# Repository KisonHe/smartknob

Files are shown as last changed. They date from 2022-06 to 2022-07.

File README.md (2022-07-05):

# SmartKnob
SmartKnob is an open-source input device with software-configurable endstops and virtual detents.

A brushless gimbal motor is paired with a magnetic encoder to provide closed-loop torque feedback control, making it possible to dynamically create and adjust the feel of detents and endstops.




# Designs

## SmartKnob View
Premium SmartKnob experience. Under active development.

⚠️ **As a result of the popularity of this project, it seems like the recommended motors are unfortunately no longer available.** I expect that these motors are simply no longer in production and therefore limited stock was available. However... 👇

💡 **There is an ongoing search for new motors** and I am currently in talks with what appears to be the original motor manufacturer about getting new motors manufactured (updated as of 2022-06-26). A summary of the motor search is being kept up to date in the [wiki](https://github.com/scottbez1/smartknob/wiki/Motor-Status), and there's a long discussion in [issue #16](https://github.com/scottbez1/smartknob/issues/16) - follow along there for the latest info (or join in and help us find a good replacement, but please check the wiki to see if your suggestion has already been mentioned before posting your own comment!). Any change in motor will likely require substantial redesigns, so *don't order PCBs/printed parts until there is more clarity on the motor.*

Features:
 - 240x240 round LCD ("GC9A01"), protected by 39.5mm watch glass on rotor
 - BLDC gimbal motor, with a hollow shaft for mechanically & electrically connecting the LCD
 - Powered by ESP32-PICO-V3-02 (Lilygo TMicro32 Plus module)
 - PCB flexure and strain gauges used for press detection (haptic feedback provided via the motor)
 - 8 side-firing RGB LEDs (SK6812-SIDE-A) illuminate ring around the knob
 - USB-C (2.0) connector for 5V power and serial data/programming (CH340)
 - VEML7700 ambient light sensor for automatic backlight & LED intensity adjustment
 - Versatile back plate for mounting - use either 4x screws, or 2x 3M medium Command strips (with cutouts for accessing removal tabs after installation)
 - Front cover snaps on for easy access to the PCB

**Current status:** Not recommended for general use (mechanical and electrical revisions may be needed depending on motor/electronics availability)

### Demo video

<a href="https://www.youtube.com/watch?v=ip641WmY4pA">
    
</a>

### How it works
<a href="https://www.youtube.com/watch?v=Q76dMggUH1M">
    
</a>

### 3D CAD

Exploded view

Latest Fusion 360 Model: https://a360.co/3BzkU0n

### Build your own?

While this is a "DIY" open-source project, it is not yet a mature plug-and-play project. If you intend to build your own, note that it requires advanced soldering experience to build - very small-pitch surface-mount soldering is required (reflow or hot air recommended), and assembly is quite time-consuming and delicate. Please go into it with the expectation that you will almost certainly need to be able to troubleshoot some hardware and firmware issues yourself - I recommend reviewing/understanding the schematics and basic firmware before jumping in!

More documentation on the BOM and what parts you need to order is coming in the future - thanks so much for your interest! Follow me on [Twitter](https://twitter.com/scottbez1) for the latest updates on this and other projects.

View the latest auto-generated (untested) [Base PCB Interactive BOM](https://smartknob-artifacts.s3.us-west-1.amazonaws.com/master/electronics/view_base-ibom.html) and [Screen PCB Interactive BOM](https://smartknob-artifacts.s3.us-west-1.amazonaws.com/master/electronics/view_screen-ibom.html) (or, the combined [BOM csv](https://smartknob-artifacts.s3.us-west-1.amazonaws.com/master/electronics/view_base-bom.csv)) for electronics/hardware parts list. ⚠️ These are auto-generated from the latest untested revision on GitHub. For tested/stable/recommended artifacts, use a [release](https://github.com/scottbez1/smartknob/releases) instead.

A few miscellaneous notes in the meantime:

 - This can _probably_ be FDM 3D printed with a well-tuned printer, but the parts shown in videos/photos were MJF printed in nylon for tight tolerances and better surface finish
 - If you wanted a simpler build, you could omit the LCD and just merge the knob + glass from the model into a single STL to get a closed-top knob
 - There's limited space inside the LCD mount for wiring, and 8 wires need to fit through the hole in the center. I used 30 AWG wire-wrapping wire. Enamel-coated wire would probably work too.
 - Strain gauges are BF350-3AA, and glued in place with CA glue (I'll include video of this process in the future, but essentially I used kapton tape to pick up the strain gauge and hold it in place during curing). This has to be done after reflow soldering, and would be hard to remove/fix in case of a mistake, so MAKE SURE TO PRACTICE GLUING strain gauges to other items before attempting on the PCB!
 - The TMC6300 is _tiny_ and has a bottom pad, so I would seriously consider getting a stencil along with the PCB order. Even with the stencil I needed to manually clean up some bridging afterward; I _highly_ recommend Chip Quik NC191 gel flux, available on [Amazon](https://amzn.to/3MGDSr5) (or use this [non-affiliate link](https://www.amazon.com/Smooth-Flow-No-Clean-syringe-plunger/dp/B08KJPG3NZ) instead) or from your electronics distributor of choice. Flux is also very helpful when soldering the LCD ribbon cable to to screen PCB.
 - For breadboard prototyping, the [TMC6300-BOB](https://www.trinamic.com/support/eval-kits/details/tmc6300-bob/) is awesome and way easier to work with than the bare chip if you just want to play around with low current BLDC motors
 - For AliExpress purchases: I highly recommend **only** using AliExpress Standard Shipping (purchasing in the US). I have had multiple purchases take months or never get delivered when purchased with Cainiao or other low cost shipping options, whereas AliExpress Standard is very reliable and generally faster in my experience.
 - Make sure to check the [open issues](https://github.com/scottbez1/smartknob/issues) - this design is not yet "stable", so beware that everything may not go smoothly. I would not recommend ordering these parts yourself until the [stable release v1.0 milestone](https://github.com/scottbez1/smartknob/milestone/1) is complete, as there are some mechanical interference issues in the current revision.

Future plans:
 - consider switch to using an ESP32-S3-MINI-1 module (once Arduino core support is complete), as that would allow for direct USB HID support (for joystick/macro-pad type input to a computer)
 - Bluetooth HID support?
 - get wifi configured and working (probably MQTT?). Currently memory is an issue with the full display framebuffer sprite. PSRAM might fix this (requires newer ESP-IDF & unreleased Arduino core, and from a brief test I got horrible performance with PSRAM enabled), or the next item might help reduce memory:
 - migrate to LVGL, for better display rendering and easy support for menus, etc. Shouldn't require a full 240x240x24b framebuffer in memory, freeing some for wifi, etc.
 - integrate nanopb for structured serial data (see [splitflap protobuf protocol](https://github.com/scottbez1/splitflap/blob/1440aba54d5b0d822ec5da68762431879988d7ef/arduino/splitflap/esp32/splitflap/serial_proto_protocol.cpp) for example)
 - Home Assistant integration, or other real-world applications
 - ???
 - [Profit](https://github.com/sponsors/scottbez1/) 😉

#### Base PCB

<a href="https://smartknob-artifacts.s3.us-west-1.amazonaws.com/master/electronics/view_base-front-3d.png">
    
</a>
<a href="https://smartknob-artifacts.s3.us-west-1.amazonaws.com/master/electronics/view_base-back-3d.png">
    
</a>

Ordering notes: use white soldermask, for reflecting light from RGB LED ring around the knob. Should be 1.2mm thick (not "standard" 1.6mm).

Latest auto-generated (untested and likely broken!) artifacts⚠️:

[Schematic](https://smartknob-artifacts.s3.us-west-1.amazonaws.com/master/electronics/view_base-schematic.pdf)

[Interactive BOM](https://smartknob-artifacts.s3.us-west-1.amazonaws.com/master/electronics/view_base-ibom.html)

[PCB Packet](https://smartknob-artifacts.s3.us-west-1.amazonaws.com/master/electronics/view_base-pcb-packet.pdf)

[Gerbers](https://smartknob-artifacts.s3.us-west-1.amazonaws.com/master/electronics/view_base-jlc/gerbers.zip)

⚠️ For tested/stable/recommended artifacts, use a [release](https://github.com/scottbez1/smartknob/releases) instead.

#### Screen PCB

<a href="https://smartknob-artifacts.s3.us-west-1.amazonaws.com/master/electronics/view_screen-front-3d.png">
    
</a>
<a href="https://smartknob-artifacts.s3.us-west-1.amazonaws.com/master/electronics/view_screen-back-3d.png">
    
</a>

Ordering notes: Must be 1.2mm thick (not "standard" 1.6mm) per mechanical design.

Latest auto-generated (untested and likely broken!) artifacts⚠️:

[Schematic](https://smartknob-artifacts.s3.us-west-1.amazonaws.com/master/electronics/view_screen-schematic.pdf)

[Interactive BOM](https://smartknob-artifacts.s3.us-west-1.amazonaws.com/master/electronics/view_screen-ibom.html)

[PCB Packet](https://smartknob-artifacts.s3.us-west-1.amazonaws.com/master/electronics/view_screen-pcb-packet.pdf)

[Gerbers](https://smartknob-artifacts.s3.us-west-1.amazonaws.com/master/electronics/view_screen-jlc/gerbers.zip)

⚠️ For tested/stable/recommended artifacts, use a [release](https://github.com/scottbez1/smartknob/releases) instead.

## SmartKnob Mini
Planned for the future.

# Frequently Asked Questions (FAQ)

**How much does it cost?**

I wish I could tell you now, but I don't actually know off the top of my head. Check back soon - I've only built 1 so far, which was the result of a bunch of tinkering and prototyping over an extended period, so I don't have all the expenses tallied up yet. Certainly less than $200 in parts, and maybe closer to $100?

**Does it work with XYZ?**

Not yet. So far I've only implemented enough firmware for the demo shown in the video, so you can't actually use it for anything productive yet. The basic detent configuration API is there, but not much else. Lots of firmware work remains to be done. If you build one, I'd love your help adding support for XYZ though!

**Can I buy one as a kit or already assembled?**

Probably not? Or at least, I don't have any immediate plans to sell them myself. It's not that I don't want you to be happy, but hardware is a hard business and I just work on this stuff in my free time.

It's open source with a fairly permissive license though, so in theory anyone could start offering kits/assemblies. If someone does go down that route of selling them, note that attribution is
 _required_ (and I wouldn't say no to [royalties/tips/thanks](https://github.com/sponsors/scottbez1/) if you're in a giving mood 🙂).

## General Component Info

### Magnetic encoders

#### MT6701 (MagnTek)
Excellent sensor at a reasonable price - highly recommended. Less noisy than TLV493D, and more responsive (control loop is more stable) using SSI.

 - Lots of IO options - SSI, I2C, and ABZ - should offer good response latency
 - SSI includes CRC to validate data
 - No power-down or low-power options - may not be ideal for battery-powered devices
 - Not available from US distributors (Mouser, Digi-Key)

[Datasheet](http://www.magntek.com.cn/upload/MT6701_Rev.1.5.pdf)

[Ordering (LCSC)](https://lcsc.com/product-detail/Angle-Linear-Position-Sensors_Magn-Tek-MT6701CT-STD_C2856764.html)

#### TLV493D (Infineon)
A mediocre choice. Easy to prototype with using [Adafruit's QWIIC breakout board](https://www.adafruit.com/product/4366).

In my testing, it is a little noisy, requiring filtering/smoothing that can slow responsiveness, hurting control loop stability. Or, with less filtering, the noise
can easily be "amplified" by the derivative component in the PID motor torque controller, causing audible (and tactile) humming/buzzing.

There is also apparently a known silicon issue that causes the internal ADC to sometimes completely lock up, requiring a full reset and re-configuration. See section
5.6 in the [User Manual](https://www.infineon.com/dgdl/Infineon-TLV493D-A1B6_3DMagnetic-UM-v01_03-EN.pdf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)

    In the Master Controlled Mode (MCM) or the Fast Mode (FM) the ADC conversion may hang up. A hang up can
    be detected by:
     - Frame Counter (FRM) counter stucks and does not increment anymore.

In my experience testing 4 different Adafruit breakout boards, 2 of them (50%) regularly exhibit this lockup behavior within a minute or two of use. It is possible to detect and auto-reset (and there is code in the project to do so), but it is slow and may cause undesirable jumps/delays if the sensor locks up often.

[Datasheet](https://www.mouser.com/datasheet/2/196/Infineon_TLV493D_A1B6_DataSheet_v01_10_EN-1227967.pdf)

#### AS5600 (AMS)
A mediocre choice. Cheap breakout boards are readily available.

In my testing, it's fairly noisy (anecdotally, noisier than the TLV493d), requiring filtering/smoothing that can slow responsiveness, hurting control loop stability. Additionally, it saturates at a lower magnetic field strength than other sensors I tested, requiring a significant air gap (8-10mm) when used with a strong neodymium diametric magnet like [Radial Magnets 8995](https://www.digikey.com/en/products/detail/radial-magnets-inc/8995/5126077).

[Datasheet](https://ams.com/documents/20143/36005/AS5600_DS000365_5-00.pdf)

### Motor drivers
#### TMC6300-LA
This is a relatively new IC and it's a perfect match! There generally aren't any other drivers (with integrated fets) that meet the requirements for the low-voltage and low-current motors used in this project (DRV8316 might work, but has not been tested).

Highlights:
 - 2-11V DC motor supply input
 - Up to 1.2A RMS
 - Tiny (3x3mm QFN)

 [Datasheet](https://www.trinamic.com/fileadmin/assets/Products/ICs_Documents/TMC6300_datasheet_rev1.07.pdf)

 [Product page](https://www.trinamic.com/products/integrated-circuits/details/tmc6300-la/)

### Motors
#### 32mm Rotor, Hollow Shaft, Diametric magnet



- 32mm rotor
- 15mm overall height (including magnet), 12.75mm height w/o magnet, 9mm rotor height
- low/zero cogging - excellent for completely smooth input
- 5.9mm hollow shaft
- built-in diametric magnet for encoder
- Proven option

This is overall the easiest motor to get started with. Low cogging and a built-in diametric magnet are great!

Sadly, does not seem to be available any longer.

# Firmware
TODO: document this

Also TODO: implement a lot more of the firmware

# Acknowledgements
This project was greatly inspired by Jesse Schoch's video "[haptic textures and virtual detents](https://www.youtube.com/watch?v=1gPQfDkX3BU)" and the
corresponding [discussion in the SimpleFOC community](https://community.simplefoc.com/t/haptic-textures/301). Seriously, this project wouldn't exist if not for that video - thank you Jesse!

# License

This project is licensed under Apache v2 (software, electronics, documentation) and Creative Commons Attribution 4.0 (hardware/mechanical) (see [LICENSE.txt](LICENSE.txt) and [Creative Commons](https://creativecommons.org/licenses/by/4.0/)).

    Copyright 2022 Scott Bezek
    
    Licensed under the Apache License, Version 2.0 (the "License");
    you may not use this file except in compliance with the License.
    You may obtain a copy of the License at
    
        http://www.apache.org/licenses/LICENSE-2.0
    
    Unless required by applicable law or agreed to in writing, software
    distributed under the License is distributed on an "AS IS" BASIS,
    WITHOUT WARRANTIES OR CONDITIONS OF ANY KIND, either express or implied.
    See the License for the specific language governing permissions and
    limitations under the License.

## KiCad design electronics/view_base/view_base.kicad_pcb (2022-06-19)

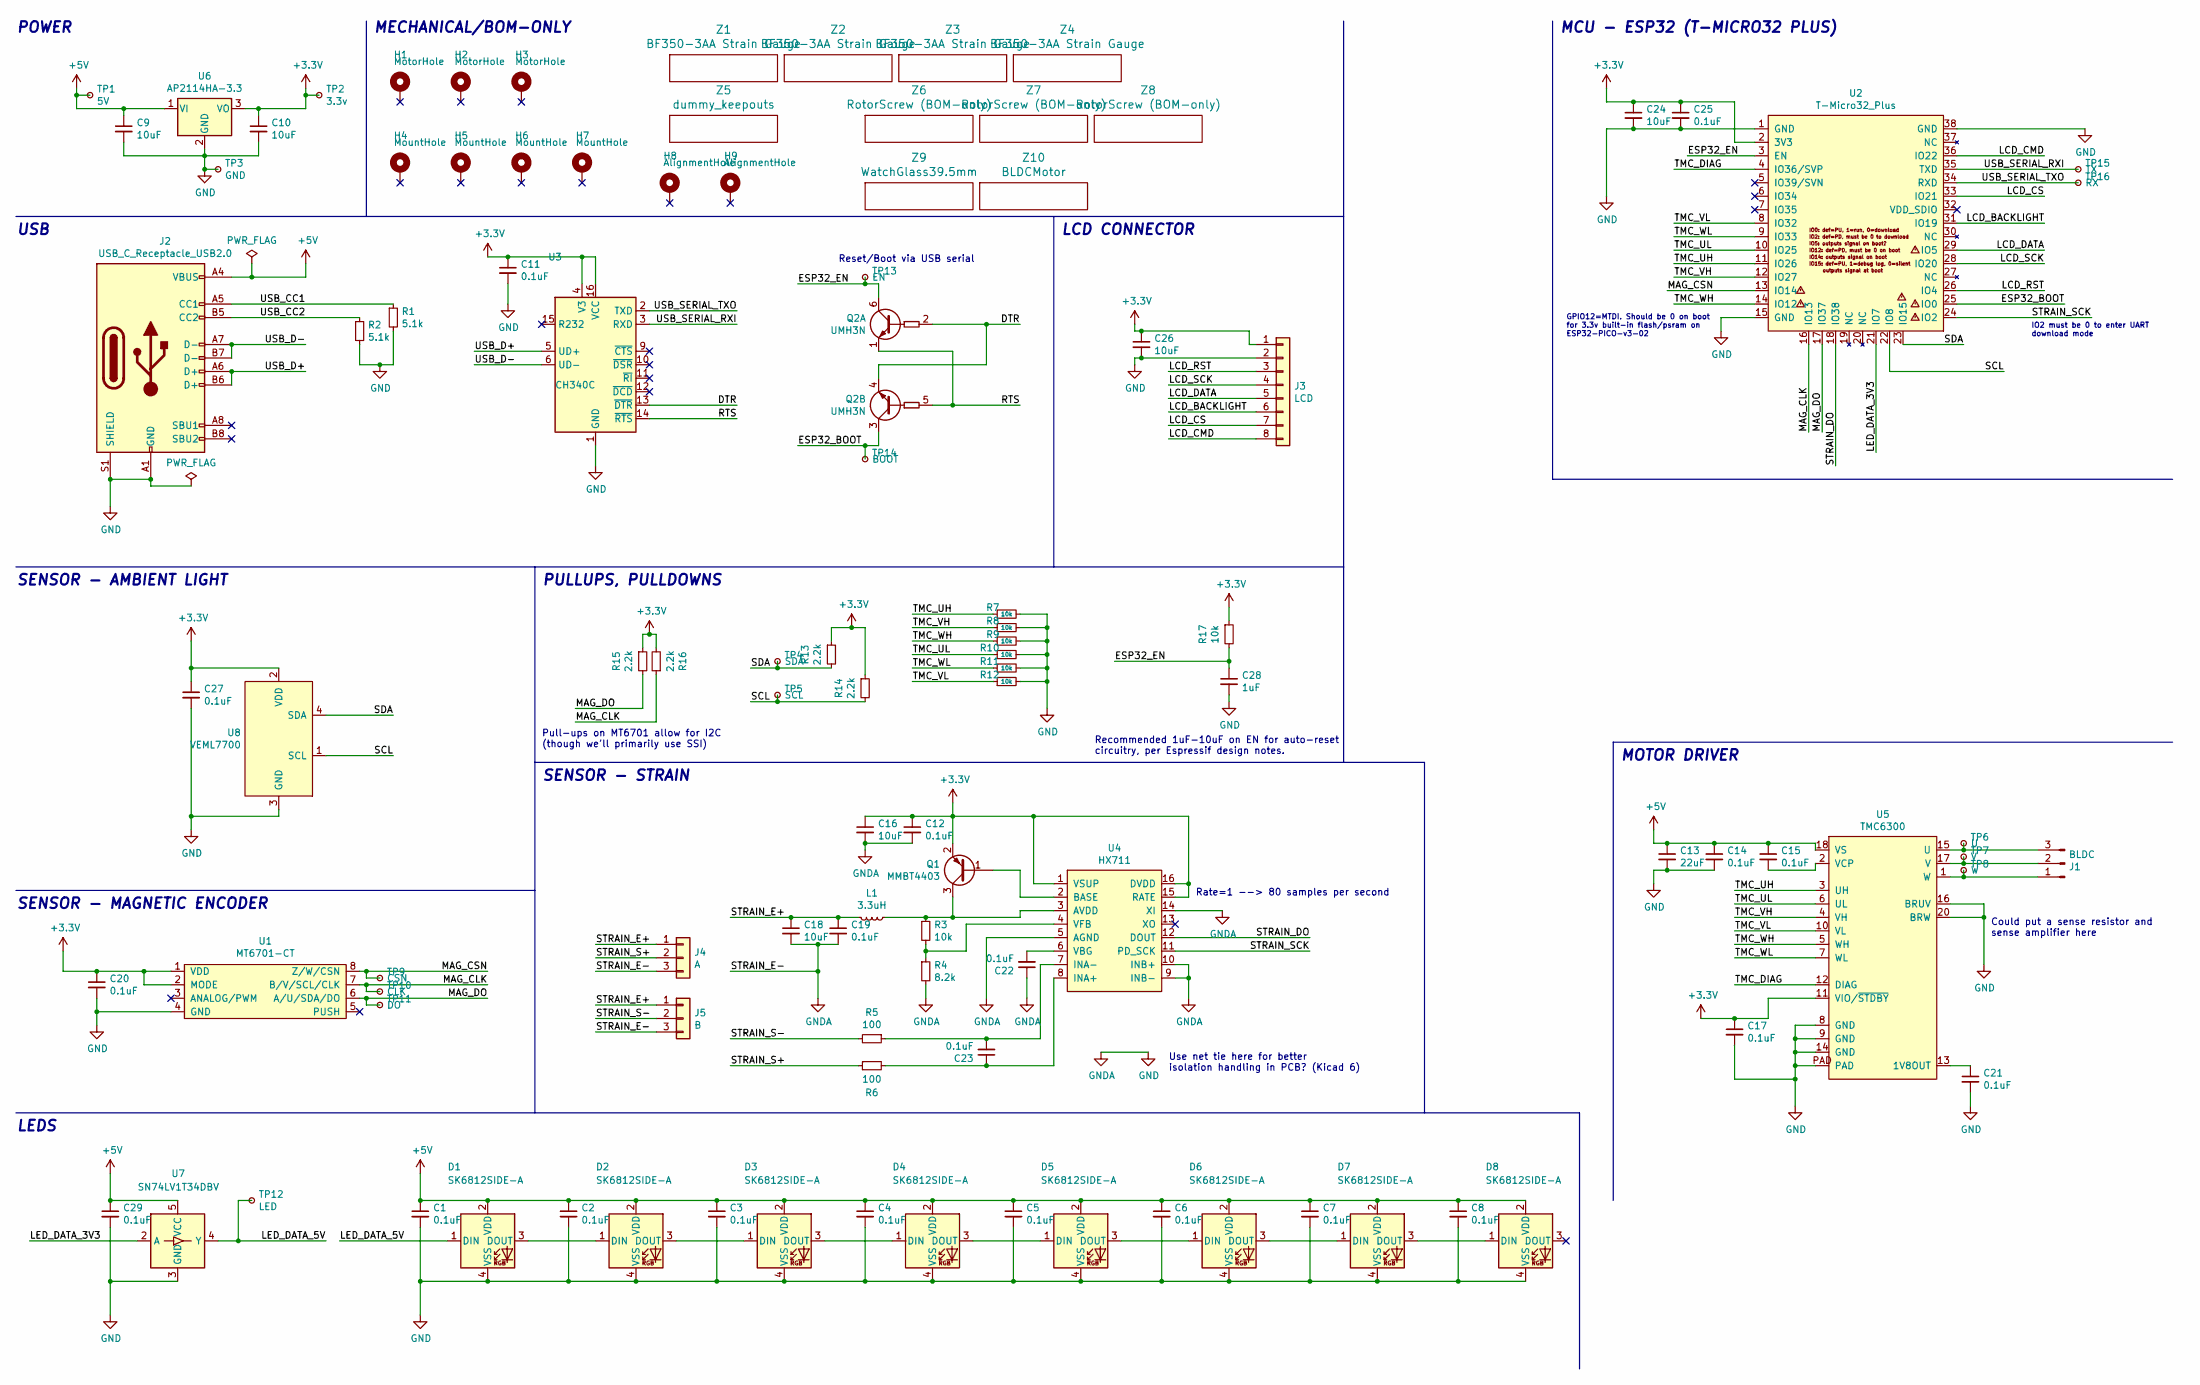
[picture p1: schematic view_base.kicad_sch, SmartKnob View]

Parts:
C1, C2, C3, C4, C5, C6, C7, C8, C11, C12, C14, C15, C17, C19, C20, C21, C22, C23, C25, C27, C29: 0.1uF; C_0603_1608Metric; LCSC C1591
C9, C10, C16, C18, C24, C26: 10uF; C_0805_2012Metric; LCSC C2922480
C13: 22uF; C_0805_2012Metric; LCSC C98190
C28: 1uF; C_0603_1608Metric; Mouser 187-CL10A105KA8NNNC
D1, D2, D3, D4, D5, D6, D7, D8: SK6812SIDE-A; SK6812-SIDE-A; Digikey 1528-4691-ND
H1, H2, H3: MotorHole; MountingHole_M1.6
H4, H5, H6, H7: MountHole; MountingHole_2.2mm_M2_ISO7380_Pad_NonVirtual
H8, H9: AlignmentHole; MountingHole_2.2mm_M2_ISO7380_Pad_NonVirtual
J1: BLDC; 532610371; LCSC C293630
J2: USB_C_Receptacle_USB2.0; USB4510_NoPaste; LCSC C428463
J3: LCD; SolderPads_2mm_8
J4: A; SolderPads_2mm_3_STRAIN
J5: B; SolderPads_2mm_3_STRAIN
L1: 3.3uH; L_0805_2012Metric; LCSC C307744
Q1: MMBT4403; SOT-23; LCSC C78864
Q2: UMH3N; SOT-363_SC-70-6; LCSC C62892
R1, R2: 5.1k; R_0603_1608Metric; LCSC C105580
R3, R7, R8, R9, R10, R11, R12, R17: 10k; R_0603_1608Metric; LCSC C98220
R4: 8.2k; R_0603_1608Metric; LCSC C114637
R5, R6: 100; R_0603_1608Metric; LCSC C319953
R13, R14, R15, R16: 2.2k; R_0603_1608Metric; LCSC C4190
TP1: 5V; TestPoint_Pad_D2.0mm_ValueSilk
TP2: 3.3v; TestPoint_Pad_D2.0mm_ValueSilk
TP3: GND; TestPoint_Pad_D2.0mm_ValueSilk
TP4: SDA; TestPoint_Pad_D2.0mm_ValueSilk
TP5: SCL; TestPoint_Pad_D2.0mm_ValueSilk
TP6: U; TestPoint_Pad_D2.0mm_ValueSilk
TP7: V; TestPoint_Pad_D2.0mm_ValueSilk
TP8: W; TestPoint_Pad_D2.0mm_ValueSilk
TP9: CSN; TestPoint_Pad_D2.0mm_ValueSilk
TP10: CLK; TestPoint_Pad_D2.0mm_ValueSilk
TP11: DO; TestPoint_Pad_D2.0mm_ValueSilk
TP12: LED; TestPoint_Pad_D2.0mm_ValueSilk
TP13: EN; TestPoint_Pad_D2.0mm_ValueSilk
TP14: BOOT; TestPoint_Pad_D2.0mm_ValueSilk
TP15: TX; TestPoint_Pad_D2.0mm_ValueSilk
TP16: RX; TestPoint_Pad_D2.0mm_ValueSilk
U1: MT6701-CT; SOIC-8_3.9x4.9mm_P1.27mm; LCSC C2856764
U2: T-Micro32_Plus; T-Micro32; Digikey N/A
U3: CH340C; SOIC-16_3.9x9.9mm_P1.27mm; LCSC C84681
U4: HX711; SOIC-16_3.9x9.9mm_P1.27mm; LCSC C43656
U5: TMC6300; QFN-20-1EP_3x3mm_P0.4mm_EP1.65x1.65mm_ThermalVias_LargerVia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; Digikey TMC6300-LA-T
U6: AP2114HA-3.3; SOT-223-3_TabPin2; LCSC C460314
U7: SN74LV1T34DBV; SOT-23-5; LCSC C100024
U8: VEML7700; VEML7700-TOP; Digikey VEML7700-TT
Z1, Z2, Z3, Z4: BF350-3AA Strain Gauge; BF350-3AA; Digikey N/A
Z5: dummy_keepouts; ViewKeepouts3d
Z6, Z7, Z8: RotorScrew (BOM-only); bom_only_no_pin
Z9: WatchGlass39.5mm; bom_only_no_pin
Z10: BLDCMotor; bom_only_no_pin

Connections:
+3V3: C10.1, C11.1, C12.1, C16.1, C17.1, C20.1, C24.1, C25.1, C26.1, C27.1, J3.1, Q1.2 (E), R13.1, R14.1, R15.1, R16.2, R17.1, TP2.1, U1.1 (VDD), U1.2 (MODE), U2.2 (3V3), U3.4 (V3), U3.16 (VCC), U4.1 (VSUP), U4.15 (RATE), U4.16 (DVDD), U5.11 (VIO/~STDBY), U6.3 (VO), U8.2 (VDD)
+5V: C1.1, C2.1, C3.1, C4.1, C5.1, C6.1, C7.1, C8.1, C9.1, C13.1, C14.1, C15.1, C29.1, D1.2 (VDD), D2.2 (VDD), D3.2 (VDD), D4.2 (VDD), D5.2 (VDD), D6.2 (VDD), D7.2 (VDD), D8.2 (VDD), J2.A4 (VBUS), J2.A9 (VBUS), J2.B4 (VBUS), J2.B9 (VBUS), TP1.1, U5.18 (VS), U6.1 (VI), U7.5 (VCC)
/DTR: Q2.2 (B1), Q2.4 (E2), U3.13 (~DTR)
/ESP32_BOOT: Q2.3 (C2), TP14.1, U2.25 (IO0)
/ESP32_EN: C28.1, Q2.6 (C1), R17.2, TP13.1, U2.3 (EN)
/LCD_BACKLIGHT: J3.6, U2.31 (IO19)
/LCD_CMD: J3.8, U2.36 (IO22)
/LCD_CS: J3.7, U2.33 (IO21)
/LCD_DATA: J3.5, U2.29 (IO5)
/LCD_RST: J3.3, U2.26 (IO4)
/LCD_SCK: J3.4, U2.28 (IO20)
/LED_DATA_3V3: U2.21 (IO7), U7.2 (A)
/LED_DATA_5V: D1.1 (DIN), TP12.1, U7.4 (Y)
/MAG_CLK: R16.1, TP10.1, U1.7 (B/V/SCL/CLK), U2.16 (IO13)
/MAG_CSN: TP9.1, U1.8 (Z/W/CSN), U2.13 (IO14)
/MAG_DO: R15.2, TP11.1, U1.6 (A/U/SDA/DO), U2.17 (IO37)
/RTS: Q2.1 (E1), Q2.5 (B2), U3.14 (~RTS)
/SCL: R14.2, TP5.1, U2.22 (IO8), U8.1 (SCL)
/SDA: R13.2, TP4.1, U2.23 (IO15), U8.4 (SDA)
/STRAIN_DO: U2.18 (IO38), U4.12 (DOUT)
/STRAIN_E+: C18.1, C19.1, J4.1, J5.1, L1.2
/STRAIN_S+: J4.2, R6.1
/STRAIN_S-: J5.2, R5.2
/STRAIN_SCK: U2.24 (IO2), U4.11 (PD_SCK)
/TMC_DIAG: U2.4 (IO36/SVP), U5.12 (DIAG)
/TMC_UH: R7.1, U2.11 (IO26), U5.3 (UH)
/TMC_UL: R10.1, U2.10 (IO25), U5.6 (UL)
/TMC_VH: R8.1, U2.12 (IO27), U5.4 (VH)
/TMC_VL: R12.1, U2.8 (IO32), U5.10 (VL)
/TMC_WH: R9.1, U2.14 (IO12), U5.5 (WH)
/TMC_WL: R11.1, U2.9 (IO33), U5.7 (WL)
/USB_CC1: J2.A5 (CC1), R1.1
/USB_CC2: J2.B5 (CC2), R2.1
/USB_D+: J2.A6 (D+), J2.B6 (D+), U3.5 (UD+)
/USB_D-: J2.A7 (D-), J2.B7 (D-), U3.6 (UD-)
/USB_SERIAL_RXI: TP15.1, U2.35 (TXD), U3.3 (RXD)
/USB_SERIAL_TXO: TP16.1, U2.34 (RXD), U3.2 (TXD)
GND: C1.2, C2.2, C3.2, C4.2, C5.2, C6.2, C7.2, C8.2, C9.2, C10.2, C11.2, C12.2, C13.2, C14.2, C16.2, C17.2, C18.2, C19.2, C20.2, C21.2, C22.1, C24.2, C25.2, C26.2, C27.2, C28.2, C29.2, D1.4 (VSS), D2.4 (VSS), D3.4 (VSS), D4.4 (VSS), D5.4 (VSS), D6.4 (VSS), D7.4 (VSS), D8.4 (VSS), J2.A1 (GND), J2.A12 (GND), J2.B1 (GND), J2.B12 (GND), J2.S1 (SHIELD), J3.2, J4.3, J5.3, R1.2, R2.2, R4.2, R7.2, R8.2, R9.2, R10.2, R11.2, R12.2, TP3.1, U1.4 (GND), U2.1 (GND), U2.15 (GND), U2.38 (GND), U3.1 (GND), U4.5 (AGND), U4.9 (INB-), U4.10 (INB+), U4.14 (XI), U5.8 (GND), U5.9 (GND), U5.14 (GND), U5.16 (BRUV), U5.20 (BRW), U5.PAD, U6.2 (GND), U7.3 (GND), U8.3 (GND)
unnamed: C15.2, U5.2 (VCP)
unnamed: C21.1, U5.13 (1V8OUT)
unnamed: C22.2, U4.6 (VBG)
unnamed: C23.1, R6.2, U4.8 (INA+)
unnamed: C23.2, R5.1, U4.7 (INA-)
unnamed: D1.3 (DOUT), D2.1 (DIN)
unnamed: D2.3 (DOUT), D3.1 (DIN)
unnamed: D3.3 (DOUT), D4.1 (DIN)
unnamed: D4.3 (DOUT), D5.1 (DIN)
unnamed: D5.3 (DOUT), D6.1 (DIN)
unnamed: D6.3 (DOUT), D7.1 (DIN)
unnamed: D7.3 (DOUT), D8.1 (DIN)
unnamed: J1.1, TP8.1, U5.1 (W)
unnamed: J1.2, TP7.1, U5.17 (V)
unnamed: J1.3, TP6.1, U5.15 (U)
unnamed: L1.1, Q1.3 (C), R3.1, U4.3 (AVDD)
unnamed: Q1.1 (B), U4.2 (BASE)
unnamed: R3.2, R4.1, U4.4 (VFB)

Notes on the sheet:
Pull-ups on MT6701 allow for I2C (though we'll primarily use SSI)
Rate=1 --> 80 samples per second
Reset/Boot via USB serial
PULLUPS, PULLDOWNS
SENSOR - AMBIENT LIGHT
MCU - ESP32 (T-MICRO32 PLUS)
MOTOR DRIVER
SENSOR - STRAIN
LEDS
POWER
SENSOR - MAGNETIC ENCODER
USB
IO2 must be 0 to enter UART download mode
Recommended 1uF-10uF on EN for auto-reset circuitry, per Espressif design notes.
MECHANICAL/BOM-ONLY
GPIO12=MTDI. Should be 0 on boot for 3.3v built-in flash/psram on ESP32-PICO-v3-02
LCD CONNECTOR
Use net tie here for better isolation handling in PCB? (Kicad 6)
Could put a sense resistor and sense amplifier here

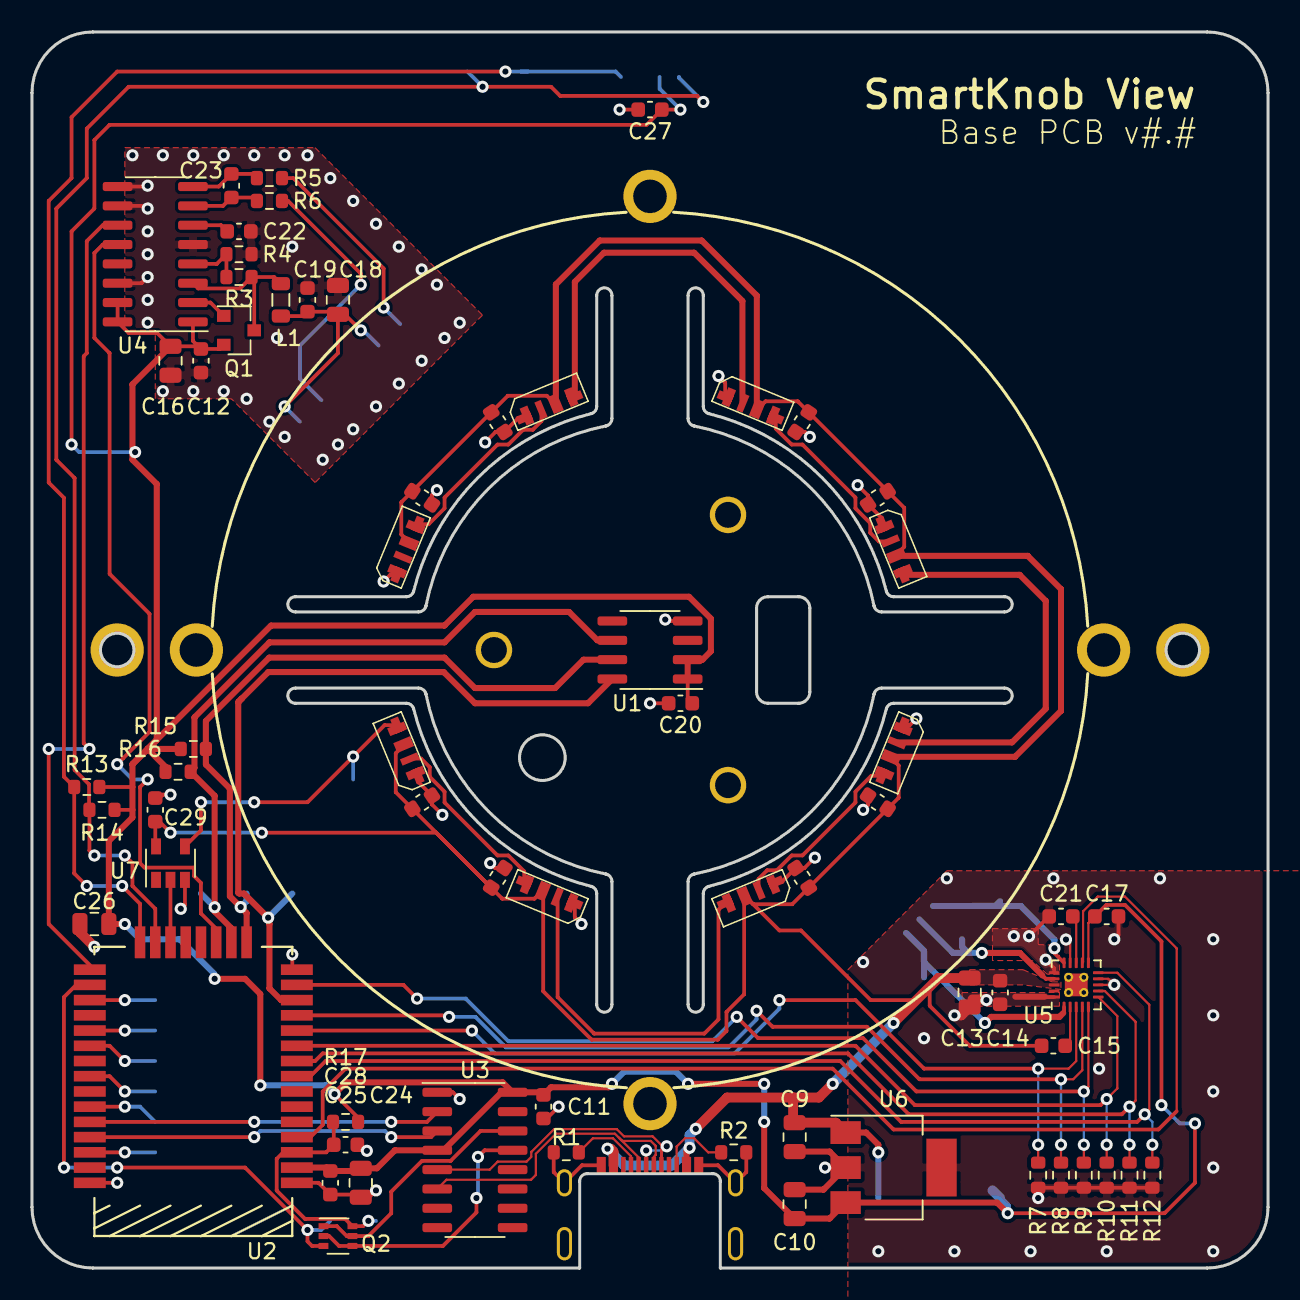
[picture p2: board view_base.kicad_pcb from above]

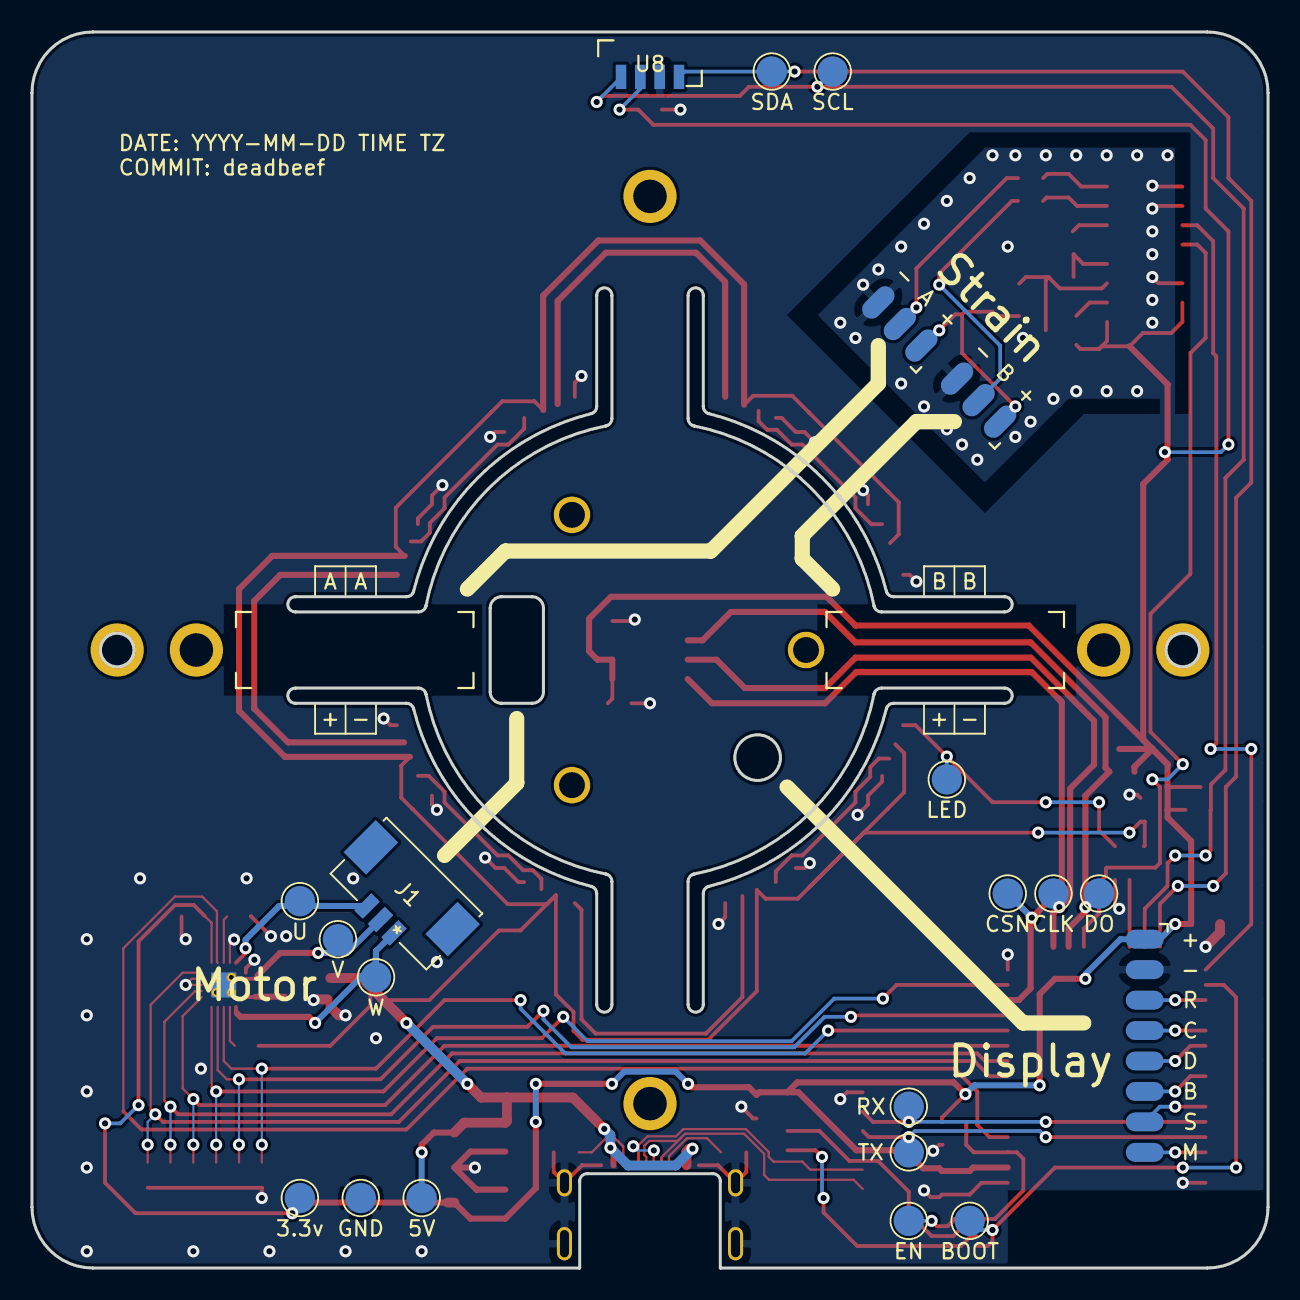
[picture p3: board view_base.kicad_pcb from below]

Board: 2 copper layers, 81.2 x 81.2 mm, 105 parts (25 on the bottom side), 56 nets.

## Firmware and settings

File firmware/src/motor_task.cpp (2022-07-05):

#include <SimpleFOC.h>
#include <sensors/MagneticSensorI2C.h>

#include "motor_task.h"
#include "mt6701_sensor.h"
#include "tlv_sensor.h"
#include "util.h"

static const float DEAD_ZONE_DETENT_PERCENT = 0.2;
static const float DEAD_ZONE_RAD = 1 * _PI / 180;

static const float IDLE_VELOCITY_EWMA_ALPHA = 0.001;
static const float IDLE_VELOCITY_RAD_PER_SEC = 0.05;
static const uint32_t IDLE_CORRECTION_DELAY_MILLIS = 500;
static const float IDLE_CORRECTION_MAX_ANGLE_RAD = 5 * PI / 180;
static const float IDLE_CORRECTION_RATE_ALPHA = 0.0005;


MotorTask::MotorTask(const uint8_t task_core) : Task("Motor", 2048, 1, task_core) {
    queue_ = xQueueCreate(5, sizeof(Command));
    assert(queue_ != NULL);
}

MotorTask::~MotorTask() {}


// BLDC motor & driver instance
BLDCMotor motor = BLDCMotor(1);
BLDCDriver6PWM driver = BLDCDriver6PWM(PIN_UH, PIN_UL, PIN_VH, PIN_VL, PIN_WH, PIN_WL);

#if SENSOR_TLV
    TlvSensor encoder = TlvSensor();
#elif SENSOR_MT6701
    MT6701Sensor encoder = MT6701Sensor();
#endif
// MagneticSensorI2C tlv = MagneticSensorI2C(AS5600_I2C);

Commander command = Commander(Serial);


void doMotor(char* cmd) { command.motor(&motor, cmd); }

void MotorTask::run() {
    // Hardware-specific configuration:
    // TODO: make this easier to configure
    // Tune zero offset to the specific hardware (motor + mounted magnetic sensor).
    // SimpleFOC is supposed to be able to determine this automatically (if you omit params to initFOC), but
    // it seems to have a bug (or I've misconfigured it) that gets both the offset and direction very wrong!
    // So this value is based on experimentation.
    // TODO: dig into SimpleFOC calibration and find/fix the issue
    // float zero_electric_offset = -0.6; // original proto
    //float zero_electric_offset = 0.4; // handheld 1
    // float zero_electric_offset = -0.8; // handheld 2
    // float zero_electric_offset = 2.93; //0.15; // 17mm test
    // float zero_electric_offset = 0.66; // 15mm handheld
    float zero_electric_offset = 7;
    // float zero_electric_offset = 2.19;
    Direction foc_direction = Direction::CW;
    motor.pole_pairs = 7;

    driver.voltage_power_supply = 5;
    driver.init();

    #if SENSOR_TLV
    encoder.init(Wire, false);
    #endif

    #if SENSOR_MT6701
    encoder.init();
    // motor.LPF_angle = LowPassFilter(0.05);
    #endif
    // motor.LPF_current_q = {0.01};

    motor.linkDriver(&driver);

    motor.controller = MotionControlType::torque;
    motor.voltage_limit = 5;
    motor.velocity_limit = 10000;
    motor.linkSensor(&encoder);

    // Not actually using the velocity loop; but I'm using those PID variables
    // because SimpleFOC studio supports updating them easily over serial for tuning.
    motor.PID_velocity.P = 4;
    motor.PID_velocity.I = 0;
    motor.PID_velocity.D = 0.04;
    motor.PID_velocity.output_ramp = 10000;
    motor.PID_velocity.limit = 10;


    motor.useMonitoring(Serial);

    motor.init();

    encoder.update();
    delay(10);

    motor.initFOC(zero_electric_offset, foc_direction);

    bool calibrate = false;

    // Serial.println("Press Y to run calibration");
    // uint32_t t = millis();
    // calibrate = true;
    // while (millis() - t < 3000) {
    //     if (Serial.read() == 'Y') {
    //         calibrate = true;
    //         break;
    //     }
    //     delay(10);
    // }
    if (calibrate) {
        motor.controller = MotionControlType::angle_openloop;
        motor.pole_pairs = 1;
        motor.initFOC(0, Direction::CW);


        float a = 0;

        for (uint8_t i = 0; i < 200; i++) {
            encoder.update();
            motor.move(a);
            delay(1);
        }
        float start_sensor = encoder.getAngle();

        for (; a < 3 * _2PI; a += 0.01) {
            encoder.update();
            motor.move(a);
            delay(1);
        }

        for (uint8_t i = 0; i < 200; i++) {
            encoder.update();
            delay(1);
        }
        float end_sensor = encoder.getAngle();


        motor.voltage_limit = 0;
        motor.move(a);
        // Serial.println("Did motor turn counterclockwise? Press Y to continue, otherwise change motor wiring and restart");
        // while (Serial.read() != 'Y') {
        //     delay(10);
        // }

        Serial.println();

        // TODO: check for no motor movement!

        Serial.print("Sensor measures positive for positive motor rotation: ");
        if (end_sensor > start_sensor) {
            Serial.println("YES, Direction=CW");
            motor.initFOC(0, Direction::CW);
        } else {
            Serial.println("NO, Direction=CCW");
            motor.initFOC(0, Direction::CCW);
        }

        // Rotate many electrical revolutions and measure mechanical angle traveled, to calculate pole-pairs
        uint8_t electrical_revolutions = 20;
        Serial.printf("Going to measure %d electrical revolutions...\n", electrical_revolutions);
        motor.voltage_limit = 5;
        motor.move(a);
        Serial.println("Going to electrical zero...");
        float destination = a + _2PI;
        for (; a < destination; a += 0.03) {
            encoder.update();
            motor.move(a);
            delay(1);
        }
        Serial.println("pause...");
        for (uint16_t i = 0; i < 1000; i++) {
            encoder.update();
            delay(1);
        }
        Serial.println("Measuring...");

        start_sensor = motor.sensor_direction * encoder.getAngle();
        destination = a + electrical_revolutions * _2PI;
        for (; a < destination; a += 0.03) {
            encoder.update();
            motor.move(a);
            delay(1);
        }
        for (uint16_t i = 0; i < 1000; i++) {
            encoder.update();
            motor.move(a);
            delay(1);
        }
        end_sensor = motor.sensor_direction * encoder.getAngle();
        motor.voltage_limit = 0;
        motor.move(a);

        if (fabsf(motor.shaft_angle - motor.target) > 1 * PI / 180) {
            Serial.println("ERROR: motor did not reach target!");
            while(1) {}
        }

        float electrical_per_mechanical = electrical_revolutions * _2PI / (end_sensor - start_sensor);
        Serial.print("Electrical angle / mechanical angle (i.e. pole pairs) = ");
        Serial.println(electrical_per_mechanical);

        int measured_pole_pairs = (int)round(electrical_per_mechanical);
        Serial.printf("Pole pairs set to %d\n", measured_pole_pairs);

        delay(1000);
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

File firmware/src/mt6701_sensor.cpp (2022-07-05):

#include "mt6701_sensor.h"
#include "driver/spi_master.h"

static const float ALPHA = 0.4;


static uint8_t tableCRC6[64] = {
 0x00, 0x03, 0x06, 0x05, 0x0C, 0x0F, 0x0A, 0x09,
 0x18, 0x1B, 0x1E, 0x1D, 0x14, 0x17, 0x12, 0x11,
 0x30, 0x33, 0x36, 0x35, 0x3C, 0x3F, 0x3A, 0x39,
 0x28, 0x2B, 0x2E, 0x2D, 0x24, 0x27, 0x22, 0x21,
 0x23, 0x20, 0x25, 0x26, 0x2F, 0x2C, 0x29, 0x2A,
 0x3B, 0x38, 0x3D, 0x3E, 0x37, 0x34, 0x31, 0x32,
 0x13, 0x10, 0x15, 0x16, 0x1F, 0x1C, 0x19, 0x1A,
 0x0B, 0x08, 0x0D, 0x0E, 0x07, 0x04, 0x01, 0x02
};

/*32-bit input data, right alignment, Calculation over 18 bits (mult. of 6) */
static uint8_t CRC6_43_18bit (uint32_t w_InputData)
{
 uint8_t b_Index = 0;
 uint8_t b_CRC = 0;

 b_Index = (uint8_t )(((uint32_t)w_InputData >> 12u) & 0x0000003Fu);

 b_CRC = (uint8_t )(((uint32_t)w_InputData >> 6u) & 0x0000003Fu);
 b_Index = b_CRC ^ tableCRC6[b_Index];

 b_CRC = (uint8_t )((uint32_t)w_InputData & 0x0000003Fu);
 b_Index = b_CRC ^ tableCRC6[b_Index];

 b_CRC = tableCRC6[b_Index];

 return b_CRC;
} 

#if SENSOR_MT6701

MT6701Sensor::MT6701Sensor() {}

void MT6701Sensor::init() {

    pinMode(PIN_MT_CSN, OUTPUT);
    digitalWrite(PIN_MT_CSN, HIGH);

  spi_bus_config_t tx_bus_config = {
      .mosi_io_num = -1,
      .miso_io_num = PIN_MT_DATA,
      .sclk_io_num = PIN_MT_CLOCK,
      .quadwp_io_num = -1,
      .quadhd_io_num = -1,
      .max_transfer_sz = 1000,
  };
  esp_err_t ret = spi_bus_initialize(HSPI_HOST, &tx_bus_config, 1);
  ESP_ERROR_CHECK(ret);

  spi_device_interface_config_t tx_device_config = {
      .command_bits=0,
      .address_bits=0,
      .dummy_bits=0,
      .mode=1,
      .duty_cycle_pos=0,
      .cs_ena_pretrans=4,
      .cs_ena_posttrans=0,
      .clock_speed_hz=4000000,
      .input_delay_ns=0,
      .spics_io_num=PIN_MT_CSN,
      .flags = 0,
      .queue_size=1,
      .pre_cb=NULL,
      .post_cb=NULL,
  };
  ret=spi_bus_add_device(HSPI_HOST, &tx_device_config, &spi_device_);
  ESP_ERROR_CHECK(ret);


  spi_transaction_.flags = SPI_TRANS_USE_RXDATA;
  spi_transaction_.length = 24;
  spi_transaction_.rxlength = 24;
  spi_transaction_.tx_buffer = NULL;
  spi_transaction_.rx_buffer = NULL;
}

float MT6701Sensor::getSensorAngle() {
    uint32_t now = micros();
    // static int cnt = 0;
    if (now - last_update_ > 100) {
      
      esp_err_t ret=spi_device_polling_transmit(spi_device_, &spi_transaction_);
      assert(ret==ESP_OK);

      uint32_t spi_32 = (spi_transaction_.rx_data[0] << 16) | (spi_transaction_.rx_data[1] << 8) | spi_transaction_.rx_data[2];
      uint32_t angle_spi = spi_32 >> 10;

      uint8_t field_status = (spi_32 >> 6) & 0x3;
      uint8_t push_status = (spi_32 >> 8) & 0x1;
      uint8_t loss_status = (spi_32 >> 9) & 0x1;

      uint8_t received_crc = spi_32 & 0x3F;
      uint8_t calculated_crc = CRC6_43_18bit(spi_32 >> 6);

      // if (cnt++%20==0)
      // {Serial.print("field_status:");Serial.println(field_status);}
      
      if (received_crc == calculated_crc) {
        float new_angle = (float)angle_spi * 2 * PI / 16384;
        float new_x = cosf(new_angle);
        float new_y = sinf(new_angle);
        x_ = new_x * ALPHA + x_ * (1-ALPHA);
        y_ = new_y * ALPHA + y_ * (1-ALPHA);
      } else {
        Serial.printf("Bad CRC. expected %d, actual %d\n", calculated_crc, received_crc);
      }

      last_update_ = now;
    }
    float rad = -atan2f(y_, x_);
    if (rad < 0) {
        rad += 2*PI;
    }
    return rad;
}

#endif

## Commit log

2022-06-19 Add comments
    [view_base.kicad_pcb, view_base.kicad_sch]
2022-07-05 New motor suffers

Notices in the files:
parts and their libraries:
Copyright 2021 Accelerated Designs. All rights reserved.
